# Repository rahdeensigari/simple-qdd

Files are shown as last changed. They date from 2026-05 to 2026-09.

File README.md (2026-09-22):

# simple-qdd
A small and cheap quasi-direct driven planetary robotic actuator. It uses an 8:1 planetary reduction powered by a 5010 BLDC drone motor recoiled in star configuration to get ~100KV.



This is not the first actuator that I have made, and it certainly won't be the last either. I was aiming to design something small and cheap that could still have a decent amount of power. In order to do this, I have to recoil a small motor that is intended to be used for drones to be more optimal for high load applications.

If you are interested in building this yourself, the BOM below is a good starting place for getting materials, but anything will similar specifications will work just as well. You can download the CAD files either directly from the Onshape document (below) or from the files listed in the CAD folder.

[CAD](https://cad.onshape.com/documents/57a8ef0242364670953218e9/w/659145295f694f0fa79f9cef/e/7b9566cf06dc05a88ad73bb1)

# BOM

| Quantity | Name | Vendor | Cost | Link | Notes  |
|---|---|---|---|---|---|
| 1 | 5010 BLDC Motor | AliExpress | $19.66  | https://www.aliexpress.us/item/3256808560627221.html  | |
| 1 | Output Bearing | AliExpress | $4.39 | https://www.aliexpress.us/item/3256807233759178.html  | |
| 3 | Needle-Roller Bearing | MCM | 23.58 | https://www.mcmaster.com/5905K496/ | |
| 7 | M3 Heatset x 3.4mm | MCM | 8.64 | https://www.mcmaster.com/94459A769/ | 1 Pack |
| 3 | M3 Heatset x 5.9mm | MCM | 5.48 | https://www.mcmaster.com/94459A421/ | 1 Pack |
| 1 | ODrive Micro | ODrive | 89 | https://shop.odriverobotics.com/products/odrive-micro | |
| 4 | M3x0.5 8mm FH | MCM | 5.82 | https://www.mcmaster.com/91294A128/ | 1 Pack |
| 4 | M3x0.5 5mm FH | MCM | 5.57 | https://www.mcmaster.com/91294A125/ | 1 Pack |
| 3 | M3x0.5 10mm FH | MCM | 6.36 | https://www.mcmaster.com/91294A130/ | 1 Pack |
| 4 | M3x0.5 10mm BH | MCM | 7.91 | https://www.mcmaster.com/92095A182/ | 1 Pack |
| 5 | M4x0.7 50mm SH | MCM | 15.85 | https://www.mcmaster.com/91290A186/ | 1 Pack |
| 5 | M4x0.7 Nuts | MCM | 13.25 | https://www.mcmaster.com/94645A101/ | |
| | | | $205.51 | | |

NOTE: A bulk of the price is because a lot of the fastners come in packs with way more of the item then is needed.

# Assembly

Main (1)


Use these exploded and section views as well as the CAD link above while assembling. Some important notes, assemble the gear carriage, the bottom retention flange, and the bearing at once before putting it into the motor carriage. Make sure the motor is fully installed in the carriage and the sun gear is installed on the motor before inserting the bearing and gear carriage assembly. Make sure the heat-set inserts in the gear carriage are fully inserted, or else the countersunk bolts won't fit correctly.

If you are going to recoil the motor, use 26 AWG magnet wire with 31 turns-per-slot if you want to get to the same KV I used. Use the following diagram when you are recoiling:


https://youtube.com/shorts/wS8en63CQcI

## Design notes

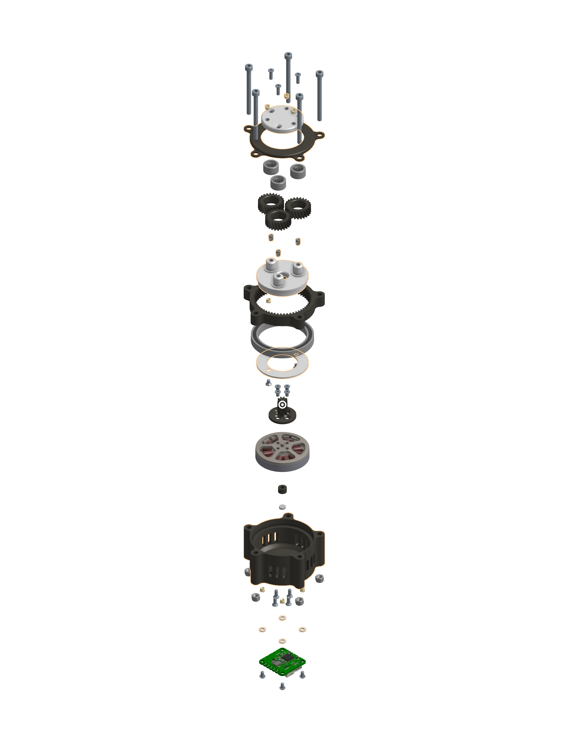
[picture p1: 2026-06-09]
docs/Exploded View.png

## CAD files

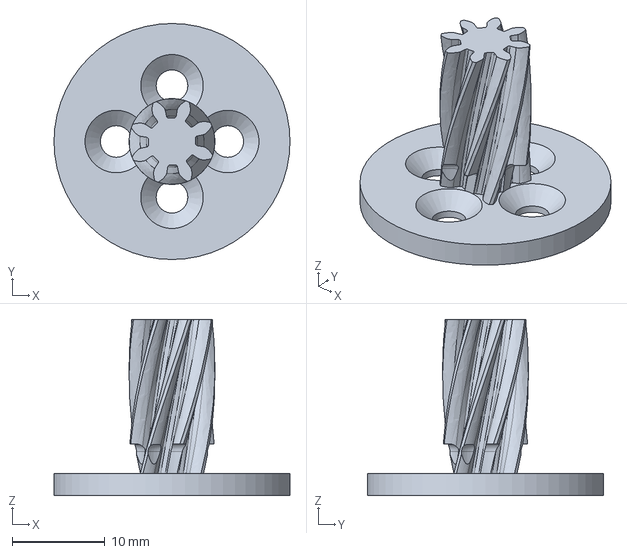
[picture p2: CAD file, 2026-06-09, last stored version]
cad/Sun Gear.step
25.4 x 25.4 x 18.9 mm

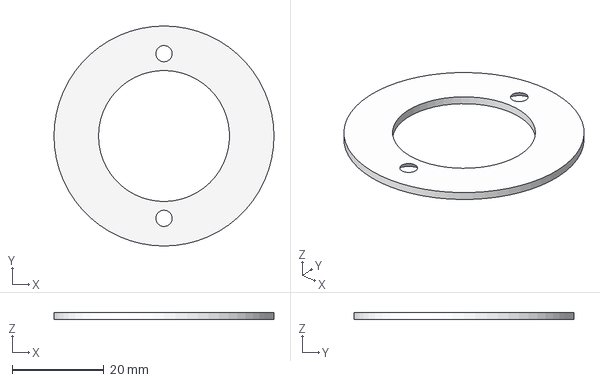
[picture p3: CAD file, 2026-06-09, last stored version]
cad/Bottom Bearing Flange.step
48.0 x 48.0 x 1.59 mm

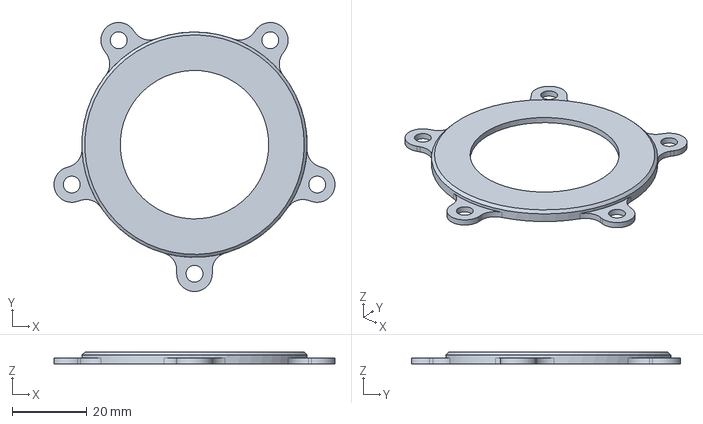
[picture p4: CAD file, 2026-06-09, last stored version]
cad/Top Cover.step
75.2 x 72.0 x 3.17 mm

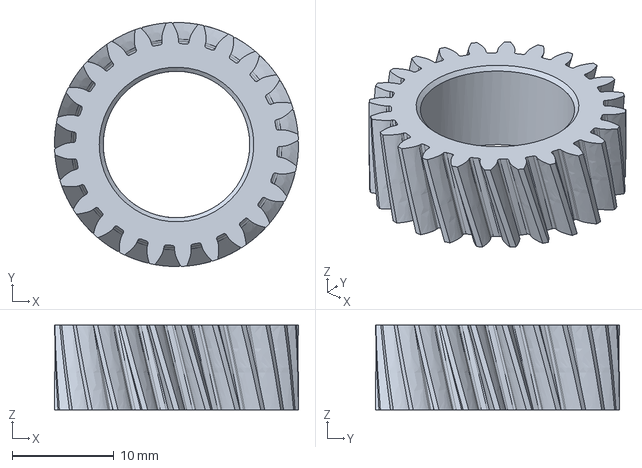
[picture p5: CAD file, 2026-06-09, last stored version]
cad/Planet Gear.step
24.0 x 24.0 x 8.33 mm

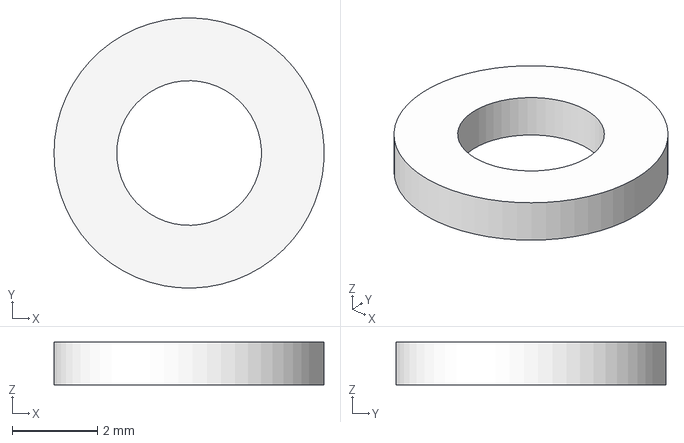
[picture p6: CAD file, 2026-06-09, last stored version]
cad/Spacer.step
6.35 x 6.35 x 1.00 mm

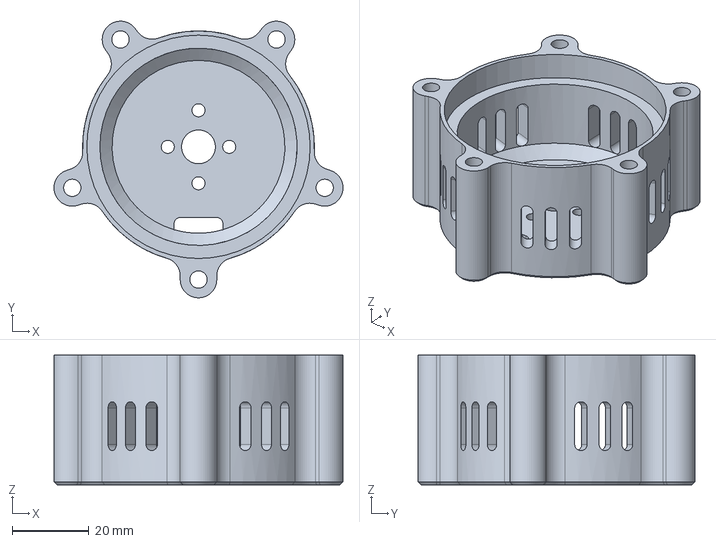
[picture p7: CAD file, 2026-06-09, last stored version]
cad/Motor Carriage.step
75.2 x 72.0 x 33.8 mm

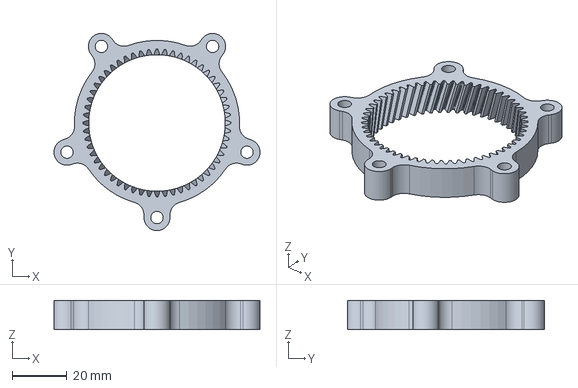
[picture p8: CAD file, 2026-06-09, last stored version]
cad/Ring Gear.step
75.2 x 72.0 x 10.7 mm

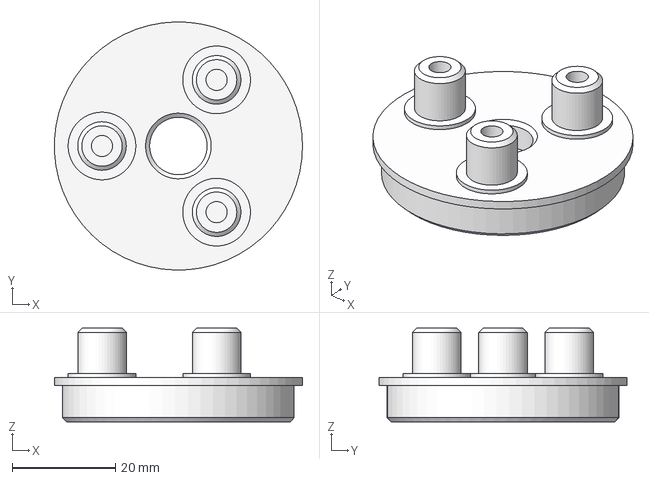
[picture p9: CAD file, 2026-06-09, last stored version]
cad/Gear Carriage.step
48.0 x 48.0 x 18.1 mm

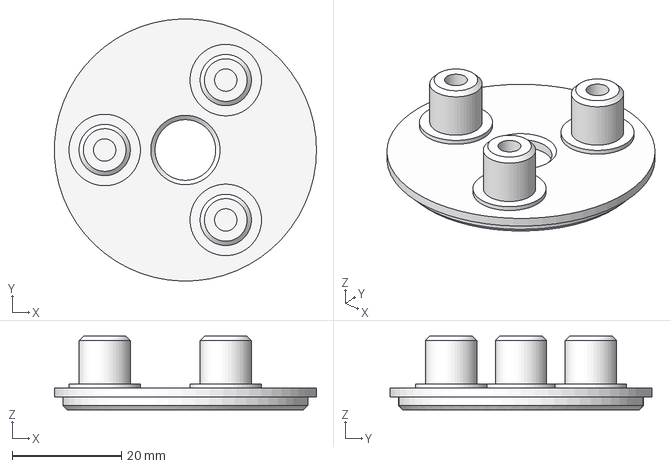
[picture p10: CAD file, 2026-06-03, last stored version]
cad/Gear Carrier.step
48.0 x 48.0 x 13.5 mm

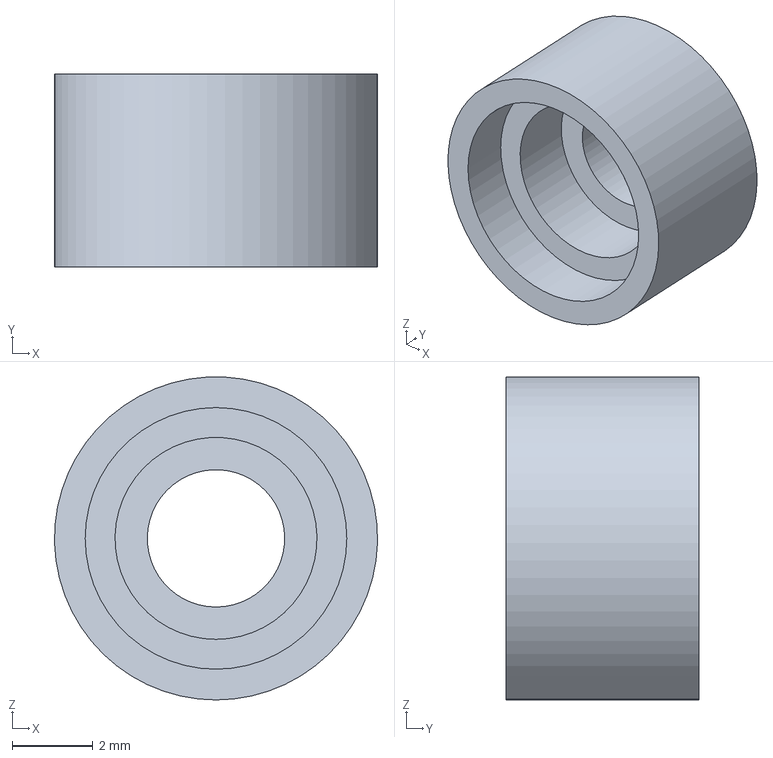
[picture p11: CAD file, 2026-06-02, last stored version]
cad/Magnet Mount.step
8.00 x 4.78 x 7.99 mm

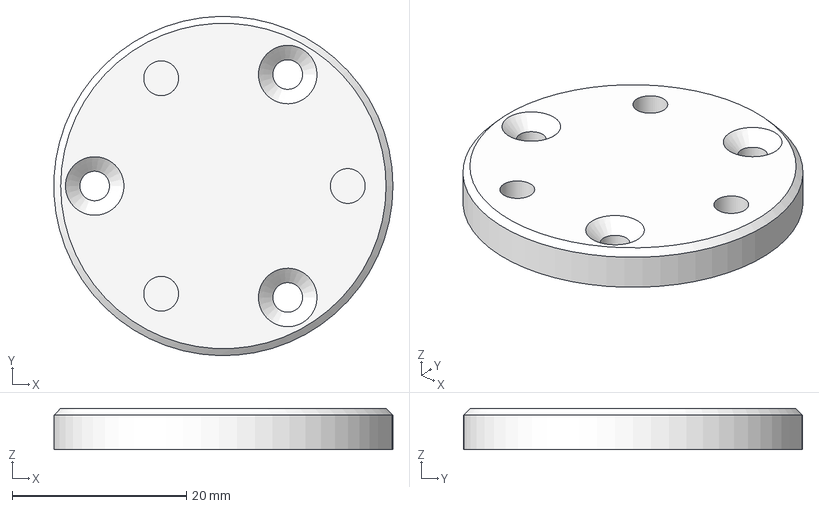
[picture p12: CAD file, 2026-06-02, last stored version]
cad/Output.step
38.9 x 38.9 x 4.76 mm

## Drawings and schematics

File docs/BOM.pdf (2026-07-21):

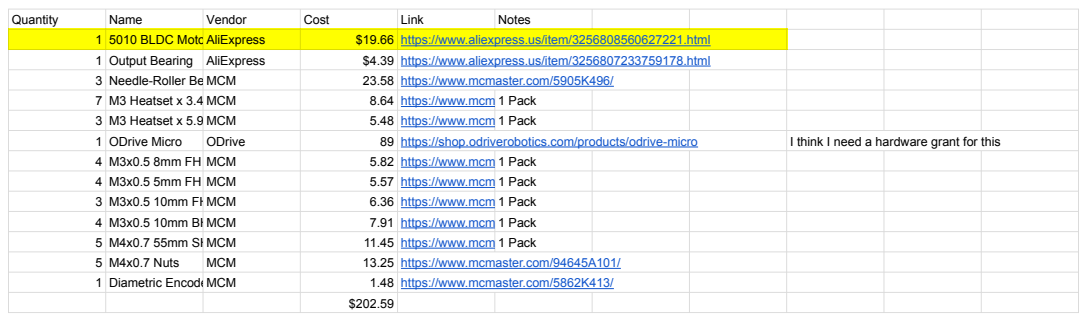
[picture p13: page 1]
Quantity; Name; Vendor; Cost; Link; Notes; 1 5010 BLDC MotorAliExpress; $19.66 https://www.aliexpress.us/item/3256808560627221.html; 1 Output Bearing AliExpress; $4.39 https://www.aliexpress.us/item/3256807233759178.html; 3 Needle-Roller Bearing MCM; 23.58 https://www.mcmaster.com/5905K496/; 7 M3 Heatset x 3.4mmMCM; 8.64 https://www.mcmaster.com/94459A769/ 1 Pack; 3 M3 Heatset x 5.9mmMCM; 5.48 https://www.mcmaster.com/94459A421/ 1 Pack; 1 ODrive Micro; ODrive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

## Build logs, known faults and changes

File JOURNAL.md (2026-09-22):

---
title: "Quasi-Direct Drive Actuator"
author: "Rahdeen Sigari"
description: "A small and cheap quasi-direct driven planetary robotic actuator."
created_at: "2026-05-09"
---

# May 9: Start

Essentially, my goal is to create a full 6-axis robotic arm, but in order to actually do that, I first need to design and build a powerful enough actuator. I've actually already built a similar actuator! Here's a photo:

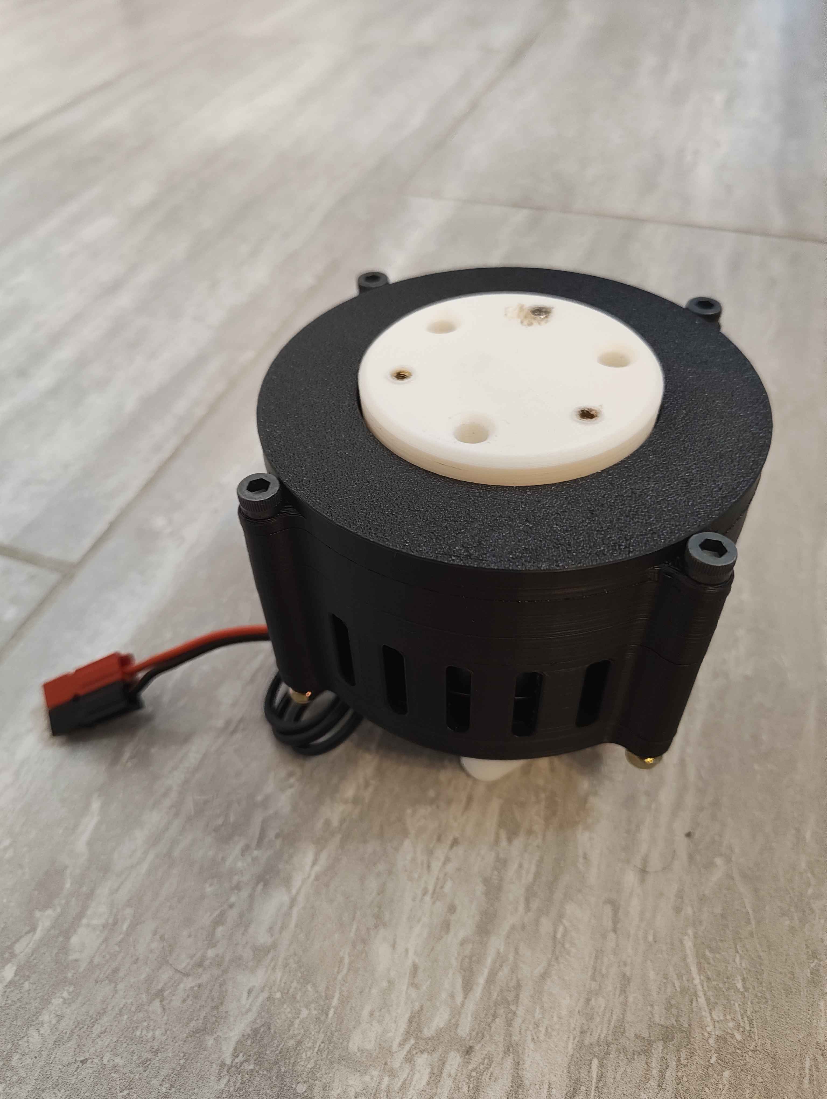
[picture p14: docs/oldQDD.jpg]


The problem with this actuator however is that it is too large, heavy, and expensive to use for an actual 6-axis arm. That's why I'm making this, a smaller, lighter, and cheaper robotic actuator that can still be powerful enough to effectively drive a robotic arm. Specifically, I want this actuator to be at most 3" in diameter.

In mechatronics applications like this, it is important for actuators to be somthing called *Quasi-Direct Drive.* Quasi-Direct Drive (QDD) actuators have a high enough gear ratio so that they can actually move signficant loads while not being so powerful that they cannot be backdriven. This is important as QDD actuators like this can completely eliminate the need for external touch sensors, as the actuator cannot overpower the external forces that are put upon it. This allows for the firmware to detect the resulting current increase and register that it has came in contact with an object.

I was kind of inspired to do this by Aaed Musa's [video](https://www.youtube.com/watch?v=GFLa1b1juUo) of him making another robot dog. He actually used something called a capstan drive, which is a gear reduction achieved by using ropes. Instead, I'm using a planetary gearbox, as it's the cheapest option and the best for small reductions like the ones in a QDD actuator as opposed to something like a cylcoidal drive. What really intrested me though was the hardware he used, specifically the motors and motor controllers. He used the following:

- Makerbase XDrive Mini (motor controller)
- TYI 5008 Brushless Motor

For my old actuator, I used:

- ODrive S1 (motor controller)
- Eaglepower LA8308 KV90 (motor)

Don't get me wrong, the hardware I bought worked excellently, but it would absurd to use them for something like a robotic arm, they're just too expensive. Luckily, the amount of power that I got from my old actuator is way more than I need for my eventual goal of making a robotic arm, as long as I keep everything else lightweight. In comparison, without accounting for extra fees, all the hardware that Aaed Musa used is $177.71 cheaper than what I used, which is absolutely absurd. For the record, if I had tried making a 6-axis arm with my old hardware, it would cost $1066.26 more!

I'm happy with the XDrive Mini as my new motor controller, but not entirely confident in the motor's strength, as it has a very high KV, which is not ideal for QDD actuators. The easiest way to fix this without increasing the gear reduction (which would result in it not being QDD anymore) is to recoil the motor stator, which I would like to avoid if I can. Will do some more research later on any alternative motors I can use.

**Total time spent: 1 hour**

# May 10: Researching Motors

I already established the TYI 5008 as good option, but its problem is mainly that it would need me to recoil the stator to decrease its KV (and subsequently increase its torque) to around 100. Ideally, I'm looking for a motor around 50mm in diameter.

- After a bit of research, I found [this](https://www.rctimer.com/rctimer-gbm5010-150t-gimbal-brushless-motor-p0446.html) motor. It is already 90KV, which means that I won't have to recoil it, but the main problem is that it is most likely too small.
- [Here's](https://rctimer.com/rctimer-5010-260kv-multirotor-brushless-motor40mm-shaft-p0132.html) another one, this one still needs to be recoiled, but the KV is much lower so it will be easier. Kind of slow shipping time though.
- [Another one](https://www.aliexpress.us/item/3256808560627221.html). This one is probably the most promising, its cheap, decent shipping time, and similar specs to the TYI 5008, of course, it will, of course, still need recoiling.

Sadly, thats all I could really find. To be honest, all these motors are pretty similar, but I think I'm going to with the third option, which is a 5010 360KV motor off Aliexpress. If I'm being honest, this is mostly because it ships the fastest out of any of the alternatives, all these motors are either 5010 or 5008 motors, and pretty much all of them except for the first one I found need to be recoiled (translation: I chose the third one based off vibes). I might buy one so that I can test its capabilites.



**Total time spent: 1 hour**

# May 11: Starting CAD (Or not)

Think I'm ready to start actually planning this out in CAD. I found [this](https://grabcad.com/library/bldc-motor-5010-1) CAD model of the motor, its supbar, but it will do for now:



Ok I did a bit more research, and I want to slightly pivot my plans. Instead of jumping straight into modeling this in CAD, I want to buy a motor first and see how well it performs, and also see its actual shape in real life as opposed to the, for lack of a better term, shitty CAD model that I found. This will let me actually CAD effectively instead of guessing. I can still work on the actual gearbox and the output stage while I wait. I've got finals to study for though so I'll save that for another time.

**Total time spent: 35 minutes**

# May 17: CAD Work

I found [this](https://grabcad.com/library/mks-odrive-mini-1) model of the motor controller, the step file that they provided did not work, so I had to import the .dwg file they gave into Fusion 360, then export that as a .step for it to work inside of OnShape:



The problem now is how I'm going to mount everything. Mounting the motor controller is pretty straight forward, really all I need are some heat-set inserts in the base motor casing that I can use to bolt it directly on. The problem is the motor itself. The CAD is very unclear about this (so is the listing on aliexpress itself) but I'm assuming that the shaft in the center of the bolt circle rotates independently from the bolt holes:



Most motors like this have some sort of bearing around the shaft, but it isn't visible in the CAD, and for some reason all the distributors of the motor seem to be allergic to giving any views other than the front of the motor, so I'm hoping this is actually how it's going to function. The best way to mount this is probably to have some countersunk holes on the bottom of the motor carriage, on the same face as the motor controller's heat-set inserts, where I can fasten the motor with some countersunk bolts. Now, for the motor controller to actually find the position that the motor is in, there needs to be a diametric magnet on the motor shaft that the motor encoder located on the back of the controller can read the position of. A diametric magnet is essentially just a magnet magnetized along its diameter as opposed to its vertical midplane. This allows the encoder to read the position of the poles, which translates to the position of the motor. [McMaster-Carr](https://www.mcmaster.com/products/magnets/direction-of-magnetization~through-diameter/) has a pretty large catalogue of diametric magnets. An 1/8" magnet will fit pretty well on the shaft of the motor. [This](https://www.mcmaster.com/5862K411/) magnet meets my specifications pretty well. It's almost the perfect size to fit directly on the shaft. I designed this small 3D printed part to mount the magnet:



I'm going to quickly print it to ensure it can be printed, it's a really small part so I'm concerned if it can be printed or not.



It printed, its so small though that I'm not sure if the parts will actually fit? If not, I will just directly glue the magnet on with a template.

I started making a layout sketch of the entire actuator, what I realized was that in order to keep a 2mm distance from the onboard motor controller and the magnet, there would only be around 1mm of clearance for a countersunk hole... which is not enough. To fix this, I'm using [this](https://www.mcmaster.com/5862K202/) magnet instead, which is a 1/16" taller. I have around 2.5mm of room now, which is definitely enough. Here is the sketch so far:



Alright it's time to talk about the gear reduction I'm using. In the past, I've used 8:1 with success, and I think I'm going to stick with 8:1 for this as well. I would like to use 4 planet gears, but it's not quite possible to get them to fit...



Which is why I'm just sticking with 3. With some playing around, I found that the perfect size for the gears are:

- Sun: 8 teeth
- Planet: 24 teeth
- Ring: 56 teeth

Using all of that, I made a (VERY!!!!) rough layout sketch of the actuator:




I very much expect to change all of this later but for now it's good enough for me to start cadding the actual parts :)

**Total time spent: 2.33 hours**

# May 18: More CAD Work - Physical Parts

I started by starting to make the motor carriage, but I think there's a very big (literally) problem:



As you can see, if I want my motor controller to fit nicely in the actuator profile, I would need to make it much larger in diameter. This would cause it go out of my 3" diameter design constraint. So, the only option would be to find a motor controller with a smaller profile. My first thought was the ODrive Mini. It's more expensive, but it has the same features as the XDrive while being much smaller plus having the added benefit of having a GUI. Another option would be to use a cheaper controller like the moteus-c1 that doesn't have UCB-C compatibility, then making my own CAN to USB-C adapter. The price difference is negligible enough that it's not worth doing that though, so I'm just going to pivot to the ODrive Micro for now. Unfortunately this means I'm going to have to change a lot of stuff. Because of this change, I can actually go back to using a 1/16" tall magnet!

Redid the layout sketch:



Didn't really journal as I was working on it so I'm just to explain what happened. I started modeling the motor carriage. Since there are components under the pcb as well, I had to slightly offset it from the base of the motor carriage. At first, I tried adding a large flange at the bottom, but it still interfered with some of the components at the very edge of the board so I'm just going to use some 3dp spacers instead:



Like I mentioned before, the motor is mounted by some countersunk bolts right below the motor controller. The actual controller is mounted with [these](https://www.mcmaster.com/94459A769/) heat-set inserts. I also started thinking about the gears. I decided to bring the dp up to 22.5 instead of 20 as that allow the pitch diameter of the ring gear to sit slightly further in from the inside of the motor carriage:



The entire assembly so far:



**Total time spent: 2.4 hours**

# May 22: CAD Work + Motor Came

Look what came today!



And, as I guessed, the CAD was inaccurate after all. Turns out where I thought there was just a nub on the bottom on the motor was actually a screw:



Because of this I have to change the magnet mount. I started by updating the CAD to be accurate:



Then I redid the magnet mount:



Then, I made the entire casing smaller, there was a lot of unnecessary extra space between the motor and the casing before that I got rid of:



Because of this, I had to increase the dp of the gears again to 27.5. The gears need a carriage to ride on, and said carriage must be able to rotate freely. This can be done using a large bearing with the carriage riding inside. For my old gearbox, I used [these](https://wcproducts.com/products/WCP-1870) bearings, and they worked wonderfully, so I'm going to continue using those. From here I moved on to modelling the sun gear. However, I encountered a problem very quickly:



The gear itself was blocking the countsink holes. To fix this, I had to have the gear itself snap fit onto the mounting base. I had to spend a lot of time figuring out a shape that I could actually print. This is what I have right now, but I'm definitely going to have to change it:



**Total time spent: 1.75 hours**

# May 24: CAD Work - Sun Gear and Gear Carriage

Continued where I left off yesterday by continuing to iterate on ways to solve the sun gear mounting problem. At first, I tried making another of a snap fit design that could actually reasonably work:



After trying to print it though, it was evident that this was not the solution, as my printer cannot print in enough detail to be able to create small features like these. Because of this, I decided to pivot to a simpler solution, which was to simply raise the gear up vertically, giving some space to get bolts into:



Testing it out, I found that because of the low amount of material at the base, it was very easy for the gear to snap off the mounting base. However, I could actually fit the bolts in the holes now with this modification. To increase the strength at the base, I kept some of the original gear profile intact:



Even with this modification, the gear was still weaker than I'm happy with. For the actual production parts I am definitely going to have to use a more ductile material like PETG instead of PLA, but PLA is fine to prototype with for now. I briefly had a problem of the clearance hole for the motor shaft in the sun gear being too short, but this was a quick fix. Here's what the gear looks like on the motor, I couldn't bolt it in because I don't have the right length flathead bolts:



Noticed this, the motor carriage is interfering with the motor. Very easy fix:



(Forgot to mention this earlier, [this](https://cad.onshape.com/documents/f349bdd78c53f3325055aefc/v/0ca31cd0b35e796be912d9e2/e/53214cbff7d86d5817cf8efb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) is the featurescript I used to generate the gear.

I then started working on the planet gear carrier. First, I made the basic shape. The flange on the bottom rests on top of the x-contact bearing, and the cutout and hole in the middle is to give the sun gear clearance:




**Total time spent: 1.32 hours**

# June 1: CAD Work

First I made the planet gear, just to get a visual of the geometry, I'm going to have to change some things about it.



So here's the problem, there are two solutions to get the gears to move smoothly with as little friction as possible. Either:

- Completely coat the carriage with a lubricant, reducing friction without the need for any external hardware.
- Have the planet gears rotate on bearings to smooth out movement.

Since this project is completely 3D printed, and I want to reduce the mess as much as possible, I'm going to go with the second option of using bearings. Now, here's the actual issue. Bearings are huge. This is what I did in my last gearbox:



The problem is that since I'm reducing the size of my gears, I don't have enough space to fit in a full sized ball bearing set into the gear. To fix this, I need to different type of bearing. I did a bit of research, and I stumbled upon [these](https://www.mcmaster.com/5905K496/) needle-roller bearings. They're technically not as smooth as ball bearings, but with some lubrication they should still work perfectly fine.

With these changes in mind, here is the planet gear I created. Unfortunately, this meant upping the heigt of the gears, and by result, the gearbox. Unfortunately just one of the results of using a stock motor for an actuator:



I then designed these extrusions on the the gear carrier for the planet gears to rotate on. The hole in the middle is for a heat-set insert.



Assembly:



I'm not modelling the motion right now because I really don't care enough to. Here's the ring gear:



Next, I mmade the output plate. There are three countersunk holes to secure it to the gear carriage, as well as three heat set inserts to mount other components to it:



Then, I made a top cover for the entire gearbox. I also added 5 M5 holes to put bolts through in order to secure the entire assembly:



I also added these "vents" so I could see the motor turning + because it looked cool:



Also, I added this wire cutout in the base of the motor carriage, without it there's nowhere for the wires to go:



With that, the CAD is actually complete! I was originally going to add a motor controller cover, but I see no need to as it would just limit my access to the port:



**Total time Spent: 3 hours**

# June 2 - Touchups and Docs

Before I start uploading all my documentation, I printed everything out just for a quick fit check.



Some problems I found:

- M3 clearance holes were too small. (For some reason I had it set to close fit?)
- The actual mounting on the motor weren't aligned with the wires. I'm not going to fix this yet because I'm going to be recoiling the motor anyways.


Everything else seems to be fine right now.

I added some stuff in my README, then created my BOM. A lot of cost comes from the fasteners, but I already have a lot of them.
| Quantity | Name | Vendor | Cost | Link | Notes  |
|---|---|---|---|---|---|
| 1 | 5010 BLDC Motor | AliExpress | $19.66  | https://www.aliexpress.us/item/3256808560627221.html  | |
| 1 | 1.75"" X-Contact | WCP | $34.99  | https://wcproducts.com/products/WCP-1870 | |
| 3 | Needle-Roller Bearing | MCM | 23.58 | https://www.mcmaster.com/5905K496/ | |
| 7 | M3 Heatset x 3.4mm | MCM | 8.64 | https://www.mcmaster.com/94459A769/ | 1 Pack |
| 3 | M3 Heatset x 5.9mm | MCM | 5.48 | https://www.mcmaster.com/94459A421/ | 1 Pack |
| 1 | ODrive Micro | ODrive | 89 | https://shop.odriverobotics.com/products/odrive-micro | |
| 4 | M3x0.5 8mm FH | MCM | 5.82 | https://www.mcmaster.com/91294A128/ | 1 Pack |
| 4 | M3x0.5 5mm FH | MCM | 5.57 | https://www.mcmaster.com/91294A125/ | 1 Pack |
| 3 | M3x0.5 10mm FH | MCM | 6.36 | https://www.mcmaster.com/91294A130/ | 1 Pack |
| 4 | M3x0.5 10mm BH | MCM | 7.91 | https://www.mcmaster.com/92095A182/ | 1 Pack |
| 5 | M4x0.7 50mm SH | MCM | 15.85 | https://www.mcmaster.com/91290A186/ | 1 Pack |
| 5 | M4x0.7 Nuts | MCM | 13.25 | https://www.mcmaster.com/94645A101/ | |
| | | | $236.11 | | |

**Total Time Spent: 1.25 hours**

# June 3 - Bearing Changes

Ok I got some opinions on using the X-Contact bearing, because it is ridiculously expensive, and I've decided that something that high quality is not needed at all. Instead, I found [this](https://www.aliexpress.us/item/3256807233759178.html) bearing on AliExpress. It's slightly different in size, so I had to change some parts to get it to fit properly, but this is definitely going to be the more cost effective option:



Here is the updated BOM:

| Quantity | Name | Vendor | Cost | Link | Notes  |
|---|---|---|---|---|---|
| 1 | 5010 BLDC Motor | AliExpress | $19.66  | https://www.aliexpress.us/item/3256808560627221.html  | |
| 1 | Output Bearing | AliExpress | $4.39 | https://www.aliexpress.us/item/3256807233759178.html  | |
| 3 | Needle-Roller Bearing | MCM | 23.58 | https://www.mcmaster.com/5905K496/ | |
| 7 | M3 Heatset x 3.4mm | MCM | 8.64 | https://www.mcmaster.com/94459A769/ | 1 Pack |
| 3 | M3 Heatset x 5.9mm | MCM | 5.48 | https://www.mcmaster.com/94459A421/ | 1 Pack |
| 1 | ODrive Micro | ODrive | 89 | https://shop.odriverobotics.com/products/odrive-micro | |
| 4 | M3x0.5 8mm FH | MCM | 5.82 | https://www.mcmaster.com/91294A128/ | 1 Pack |
| 4 | M3x0.5 5mm FH | MCM | 5.57 | https://www.mcmaster.com/91294A125/ | 1 Pack |
| 3 | M3x0.5 10mm FH | MCM | 6.36 | https://www.mcmaster.com/91294A130/ | 1 Pack |
| 4 | M3x0.5 10mm BH | MCM | 7.91 | https://www.mcmaster.com/92095A182/ | 1 Pack |
| 5 | M4x0.7 50mm SH | MCM | 15.85 | https://www.mcmaster.com/91290A186/ | 1 Pack |
| 5 | M4x0.7 Nuts | MCM | 13.25 | https://www.mcmaster.com/94645A101/ | |
| | | | $205.51 | | |

**Total Time Spent: 0.58 hours**

# June 4 - Preparing for Recoiling the Motor

Alright first, I actually forgot to include the [diametric magnet](https://www.mcmaster.com/5862K413/) in the BOM, so I quickly updated it to reflect that.

Here's the updated BOM:

| Quantity | Name | Vendor | Cost | Link | Notes  |
|---|---|---|---|---|---|
| 1 | 5010 BLDC Motor | AliExpress | $19.66  | https://www.aliexpress.us/item/3256808560627221.html  | |
| 1 | Output Bearing | AliExpress | $4.39 | https://www.aliexpress.us/item/3256807233759178.html  | |
| 3 | Needle-Roller Bearing | MCM | 23.58 | https://www.mcmaster.com/5905K496/ | |
| 7 | M3 Heatset x 3.4mm | MCM | 8.64 | https://www.mcmaster.com/94459A769/ | 1 Pack |
| 3 | M3 Heatset x 5.9mm | MCM | 5.48 | https://www.mcmaster.com/94459A421/ | 1 Pack |
| 1 | ODrive Micro | ODrive | 89 | https://shop.odriverobotics.com/products/odrive-micro | |
| 4 | M3x0.5 8mm FH | MCM | 5.82 | https://www.mcmaster.com/91294A128/ | 1 Pack |
| 4 | M3x0.5 5mm FH | MCM | 5.57 | https://www.mcmaster.com/91294A125/ | 1 Pack |
| 3 | M3x0.5 10mm FH | MCM | 6.36 | https://www.mcmaster.com/91294A130/ | 1 Pack |
| 4 | M3x0.5 10mm BH | MCM | 7.91 | https://www.mcmaster.com/92095A182/ | 1 Pack |
| 5 | M4x0.7 50mm SH | MCM | 15.85 | https://www.mcmaster.com/91290A186/ | 1 Pack |
| 5 | M4x0.7 Nuts | MCM | 13.25 | https://www.mcmaster.com/94645A101/ | |
| 1 | Diametric Encoder Magnet | MCM | 1.48 | https://www.mcmaster.com/5862K413/ | |
| | | | $206.99 | | |

Anyways, while I wait for this to be reviewed on Forge, I'm going to start doing the calculations on how I'm going to recoil the motor. To review, the motor that I have right now is wired in delta-configuration, which means that the three stator windings are connected in a closed loop that resembles a triangle. Each winding's end is connected to the other winding's beginning, making a continuous circuit. There are a couple advantages of a motor wired in delta-configuration. The main advantage of this type of winding is that it can achieve higher torque at higher speeds as opposed to star-configuration coiled motors. Although this sounds like a good thing, these motors are much less efficient at low speeds, as it draws more current for the same amount of torque. Heat generation is also increased with delta-configuration. They are ideal for high-speed applications, but for a robotic actuator, star-configuration is definitely the way to go.



Star configuration is different as all three stator windings are connected to a central point called the neutral point. This forms a star, or Y shape. The other ends of the windings are then connected to the motor controller. This configuration is better suited to give high effeciency at low speeds, which is why it is ideal for this application. A general rule between delta and star-configuration is that delta-configuration coiled motors have a $\sqrt{3}x$ higher KV then star-configuration coiled motors.



Here's the problem: If I were to recoil the motor with the exact same turns/slot and wire awg as the manufacturer, I would get ~208 KV, which is way higher than what I'm aiming for. Luckily, the KV rating is proportional to the number of turns/slot on the motor. So I can divide $208/100$ (100 being the KV I'm aiming for) to get $2.08$. This means that I have to use $2.08x$ the turns/slot to get to 100KV. Since the windings are layered on top of eacher other on my motor, counting the turns/slot is going to have to require taking apart the winidngs, so first, just to make my calculations more accurate, I'm going to find the actual KV of the motor to see if it's accurate or not. To do this I'm going to use the following formula:

$KV=RPM/(V*\sqrt{3})$

I'm multiplying the voltage by $\sqrt{3}$ because the motor is currently coiled in delta configuration. Normally you would use something like a lathe or a drill for this, but I don't have access to anything like that so I'm just going to use the motor from my old actuator. I had this old test mount laying around that I'll use:



Then I wrote this quick script to set the motor to a desired RPM:

```python
import odrive
import time

from odrive.enums import *

odrv = odrive.find_any()
axis = odrv.axis0

axis.controller.config.control_mode = ControlMode.VELOCITY_CONTROL
axis.controller.config.input_mode = InputMode.PASSTHROUGH
axis.requested_state = AxisState.CLOSED_LOOP_CONTROL

axis.controller.config.vel_limit = 30.0

time.sleep(0.5)

def set_rpm(axis, rpm):
    turns_per_sec = rpm / 60.0
    axis.controller.input_vel = turns_per_sec

def get_actual_rpm(axis):
    turns_per_sec = axis.pos_vel_mapper.vel
    return turns_per_sec * 60.0

set_rpm(axis, 500)

try:
    while True:
        print(f"Target: {axis.controller.input_vel * 60:.1f} RPM | "
            f"Actual: {get_actual_rpm(axis):.1f} RPM")
        time.sleep(0.1)

finally:
    print("Stopping motor...")
    axis.controller.input_vel = 0.0
    time.sleep(0.5)
    axis.requested_state = AxisState.IDLE
    print("Motor Stopped")
```

Alright I'm going to be honest I restarted my computer and lost an hour of progress on the journal... So if the following stuff I write isn't as detailed that's why.

I'll quickly go over how the script works:

```python
import odrive
import time

from odrive.enums import *

odrv = odrive.find_any()
axis = odrv.axis0

axis.controller.config.control_mode = ControlMode.VELOCITY_CONTROL
axis.controller.config.input_mode = InputMode.PASSTHROUGH
axis.requested_state = AxisState.CLOSED_LOOP_CONTROL

axis.controller.config.vel_limit = 30.0
```

This block is the setup. I'm importing the ODrive pip module and time, then importing all the enums from the module. Then, I'm searching to see if any ODrive boards and connected and assigning the motor to axis0. In the last 3 lines, I'm setting the control mode to velocity, the input mode to passthrough, which allows me to control it directly, and setting the axis state to closed loop control. I also set the velocity limit to 30 because by default it was capping me to 600 rpm. I'm pretty sure after you run this once, you don't need that line anymore but I kept it just incase.

```python
time.sleep(0.5)

def set_rpm(axis, rpm):
    turns_per_sec = rpm / 60.0
    axis.controller.input_vel = turns_per_sec

def get_actual_rpm(axis):
    turns_per_sec = axis.pos_vel_mapper.vel
    return turns_per_sec * 60.0

set_rpm(axis, 500)
```

The time.sleep is to give me a second before the motor start spinning. I defined two functions next, one to set the rpm that the motor will be rotating at. I have to divide by 60 because ODrive doesn't handle velocity in RPM. I'm then setting the input velocity to that new value. The get_actual_rpm function gets the encoder reading of the motor. This is to detect if there are any great disparities between the value I set and the actual RPM. I then set the RPM of the motor using the set_rpm function.

```python
try:
    while True:
        print(f"Target: {axis.controller.input_vel * 60:.1f} RPM | "
            f"Actual: {get_actual_rpm(axis):.1f} RPM")
        time.sleep(0.1)

finally:
    print("Stopping motor...")
    axis.controller.input_vel = 0.0
    time.sleep(0.5)
    axis.requested_state = AxisState.IDLE
    print("Motor Stopped")
```

This final block constantly prints the RPM I set the motor to run at and the actual RPM that the encoder detects. It's in a try-finally block because the ODrive module doesn't have a way to deal with the script being terminated by default. Honestly I didn't really need to write a script for this, I could've just used the GUI, but I needed to learn how to code for ODrive anyways so I don't mind.

I quickly modelled an adapter and test stand in CAD that allows me to connect the LA8308 (the golden motor) to the 5010 so I can test the KV. The prongs on the adapters catch each other and rotate:




This is full setup with everything printed:



I was kind of confused at first when I initally ran the motor because I had the multimeter on detecting DC current, so it was just reading 0, but after some reaearch I realized what I did wrong so I switched the multimeter to AC and tried getting readings. I tried running the motor at different RPM's to see if the results varied. Here are the results. I tried every combination of phase wires to get the most accurate result.

1000 RPM
- 1: 1.7V
- 2: 1.7V
- 3: 1.7V

500 RPM
- 1: 0.7V
- 2: 0.7V
- 3: 0.7V

1500 RPM
- 1: 2.7V
- 2: 2.7V
- 3: 2.7V

Here is the KV rating I calculated for each speed:
- 1000 RPM: 340 KV
- 500 RPM: 413 KV
- 1500 RPM: 320 KV

There's a huge difference between the values, especially at 500 RPM. This might be because it's just too slow, so I'm going to delete that data point and try again at 2000 RPM. I got 3.1V all around using 2000 RPM, which translates to 372 KV. Still a bigger difference then I would have liked, but it's not as bad anymore. Taking the average of all three values gives me 344, so not exactly 360 as the manufacturer listed. I'll be using this value for my future calculations. Now that I have the actual KV of the motor, I can go ahead with starting to take it apart.

**Total Time Spent: 3.65 hours**

# June 5 - Recoiling Calculations + Uncoiling Motor

Alright, so I completely uncoiled the motor:



As I was uncoiling it, I counted the amount of turns-per-slot and got 23. Since the KV of the motor is proportional to the turns-per-slot, I can now calculate how many I need to get 100KV:

First I need to account for the motor being in delta configuration:

$344/\sqrt{3}=199$

Then, If I divide that by the KV I want, I get the ratio of how many times more windings I need to get to my desired KV rating:

$199/100=1.99$

$1.99*23=45.8$

45.8 then rounds up to **46**, the turns-per-slot necessary.

**Total Time Spent: 0.35 hour**

# June 6 - Recoiling Attempt #1 + CAD Fixes

I got some cheap 24 AWG magnet wire today, and I tried to recoil the motor using the following diagram:



However, I believe that 24 AWG is too large of a diameter, so I am going to return the spool I got and try 26 AWG instead.

Also, I got some feedback on my design and have a couple changes to make. First, with the current design I can straight up just pull the output disc and the entire gear system will disengage from the main bearing. To fix this, I'm going to add a flange underneath the bearing as well secured by a plastic threading screw.



Here's it implemented:



I decided to not use plastic tapping screws and just use regular screws and heat set inserts as it would be cheaper.

**Total Time Spent: 1.28 hours**

# June 8 - Rewinding Attempt 2

May god help me because this is the most painful process of all time. Obviously I couldn't record journal entries as I was winding the motor, but I basically tried the same thing as before except with 26 AWG wire instead. The good news is that I can actually fit 46 windings in one slot, the bad news is that it was extremely messy and extremely difficult to wind, especially if I was winding a slot that already had another fully winded one right next to it. I technically got an entire phase wired, but I am very unhappy with the result, and I am most likely going to unwind it again. Another possible idea I have is to take out the center bearing stack by heating the adhesive holding it and the stator together. This will making rewinding the stator much easier. Here a couple photos I took of the rewinding process:






**Total Time Spent: 1.73 hours**

# June 9 - Exploded View

The project got returned because I didn't have any assembly instructions, so I'm just going to really quickly make an exploded view showing how everything fits together. Here it is, as well as a section view:

Main (1)


I'm also going to add them to the README and add a quick paragraph laying out some important points. I also updated the CAD folder with the new step files.

**Total Time Spent: 0.55 hours**

# June 19 - Added full STEP file + Updated BOM

Project got returned because I didn't have a full STEP file of the assembly included. I added it as Main.step in the cad folder. Also, because of some earlier changes I made, the retention bolts were too short so I had to up their length to 55mm. I then updated the BOM to reflect that change.



**Total Time Spent: 0.1 hours**

# July 4 - Recoiling Work

Alright, I'm back to work on this after forever! So, here's what I'm going to do. Right now, 46 turns is essentially impossible to get on the motor stator, so, unfortunately, I am going to have to settle for less turns. Instead of trying to go for 100KV, I'm instead going to settle with 150KV. Doing the calcuations again, I need around 31 turns per slot to achieve this. With that in mind, I tried recoiling one phase of the stator. It was still slightly difficult and I had to redo some individual slots a couple times but I eventually got this:



As you can see, I slightly messed up which stator slot I had to route on the last two, but it proved regardless that 31 turns were much easier to route than 46. Luckily, I was going to recoil at least the last slot anyways so it wasn't too big of a deal. I'm going to fix the mistake and continue recoiling tommorow hopefully.

**Total Time Spent: 1 hour**

# July 21 - Clarification for Reviewers

Hello, someone dm'd me on slack about this so I just want to clear it up here. Look at the PDF BOM in the docs folder please, not the CSV or the one in the readme. The parts highlighted (so just the motor for now, and potentially the ODrive if that's not applicable for funding) do **NOT** need funding, I already have the motor, as I needed to buy it beforehand to actually get the dimensions for the CAD model.

**Total Time Spent: 0 hours**

# July 23 - Starting to Build

I got my grant yesterday and ordered all of my parts. McMaster-Carr has extremely fast shipping so all of the parts from them already arrived!



If you remember, I already have all the parts printed, so I just immediately started the build. First, I put the needle bearing in the gears. The clearance was nice, so they fit in perfectly:



Next, I'm going to use my soldering iron to put all the heat-set inserts in. I encountered a pretty big problem while doing this, my heat-set insert tip on my soldering iron is very dirty, so dirty that melted plastic that it caught would get stuck in the threads of the heat-set inserts, basically making them useless. Luckily, I have an M3 tap so I literally just retapped the heat-sets, it's kinda rough but it should do. I am also going to reprint and re heat-set the output disk in white.



One more thing, there's a lot of play between the needle bearings and the internal shaft on the carriage, so I think I'm going to reprint that as well. I'm honestly just going to make that white PLA as well, I doubt that needs to be PETG-CF. As you can see, I originally subracted 0.005" so that it would fit, but this was clearly unnecessary.



I'll write a new journal entry once everything gets printed.

**Total Time Spent: 1.1 Hours**

# July 24 - Change to Gears + Assembly

Alright, so this change was from yesterday but I didn't record it, but I added a little base to the planet gears to help retain the bearings in place, as the bearings were actually slightly shorter than the gears.



With this change and all the ones from yesterday, I printed all of the parts, the gears out of PETG-CF, and the carriage and output disk out of white PLA. Then, I added heat-set inserts to all the parts that needed them and put the needle bearings into the new planet gears. Taking out the needle bearings out of the old gears was quite difficult, as they were retained very well in place, but I eventually had the idea to heat up my 3D printers bed to loosen the filament and push them out.



I also assembled the carriage with the parts that I had available. Everything rotated decently smoothly, but it will be even better with some white lithium which I will put on during the final assembly.



And for good measure, I assembled the entire shell together.



I also updated the github repo with these parts. All that's left to do now is finish rewinding the motor and wait for the other parts to arrive.

**Total Time Spent: 1.22 Hours**

# August 7 - Bearings arrived, carriage changes, recoiling

I forgot to journal most of this stuff earlier so a quick overview of what happened:

First, my bearings came!



Here's the problem: Currently in the CAD I have a slight clearance fit between the gear carriage and the bearing itself. This was done to account for 3D print inaccuracy and tolerances, however I am willing to bet that the bearing was manufactured with unilateral negative tolerances. To fix this, I am going to change the fit of the carriage to be a slight interference fit instead of clearance. I went ahead and printed it out as well. While I'm waiting for it to finish printing, I'm going to try to recoil the stator again. I've been putting this off for a while because of how annoying of a process it is, but I think I just have to bite the bullet and get it done with. Last time I tried to recoil the stator, I accidently coiled the wrong stator slots on one side, so first, I need to redo those two slots:



From there on it went pretty smoothly. Here's the second phase:



And finally the third:



Once all the phases were coiled, I soldered all their ends together at one central star point (since this is now in star configuration):



Then I soldered all my wires on and wrapped them in heatshrink:




After this, I connected the motor to my old ODrive S1 like I did earlier. For some reason, I am getting the error "PHASE_RESISTANCE_OUT_OF_RANGE" when I try to calibrate the motor. I'm really tired right now so I'll pick up trying to fix this tomorrow.

**Total Time Spent: 2.9 Hours**

# September 20 - CAD Changes

It's been a while since I've worked on this, but it seems like for some reason a lot of my journal entries are gone? A lot of stuff happened after the last journal entry, so I'm just going to quickly go over everything. The error from the last entry was fixed through some changes in the ODrive settings, and with those settings changed, everything worked fine (I believe I changed the phase resistance value in ODrive configuration to a value that I measured, but again this happened a while ago so I don't quite remember). After I got the motor to work, I tried to assemble everything, here are a couple photos:






When I tried backdriving the actuator after assembling it, the sun gear actually snapped from the base and there was way more friction then I anticipated:



I believe this happened because I didn't account for the axial thrust force that helical gears generate. I'm going to fix this today by switching to either spur or herringbone gears. I also got my design review by a couple of people and I have a general idea of some other changes that I want to make.

The first thing I did was to make all of the gears spur gears. I started with the sun gear, and this was pretty straightforward. Having it be a spur gear also made making the cutouts for the screws much easier:



The bad thing was that this broke a LOT of my features, but most of these were just changing the reference:



The other gears were also really straightforward, nothing really noteworthy except for having to change more references:



I also had to update the assemblies to match:



The next issue was that there was no clearance between the planet gears and the output disk:



I was initially going to print separate washers entirely to space them apart, but instead I decided on a different approach and just added spacers fused to the bottom of the output disk:




I also went ahead and beefed up the base of the sun gear with some extra material:



Honestly, that's all the changes that I can realistically make while still staying in scope. There's a lot of stuff that I want to change but can't quite do right now, but I will certainly keep in mind when designing another actuator like this in the future (credit to BitSentinel and Eliot):

- An output bearing at the top of the actuator as well as one for the carriage.
- Using a bigger motor controller like I planned on doing before.
- Heatsinking for the motor controllers and the motor.
- Needle bearings must be rolling on a hardened steel shaft, not a 3D print or even an aluminum part.

For now though, I think these changes will be sufficient. I'm going to go ahead and print out all of the changed parts.

First, the output disk. I'm printing this first because I already have white filament loaded on my printer. I'm going to be using 5 walls, 30% gyroid infill for this part and print it out of basic PLA:




Next, I printed all of the changed gears. I'm also going to be printing these with 5 walls, 30% gyroid out of PETG-CF:


(I printed the other two gears later)

I also went ahead and added heatsets to the output disk while I was waiting for everything else to print:



Once everything printed, I first started by putting on the new sun gear. One of the bolts didn't align for some reason? But it works fine so I don't care too much:



Then, I bolted the motor into the body of the actuator:



And assembled the carriage:





I then proceeded to add the needle bearing carriers to the new gears. Getting these on were a pain, I literally had to use the bottom of a water bottle to press them in:



After I assembled these on the carriage, I noticed something a bit weird, and that was that for some reason the sun gear and the planets didn't line up? I have no idea why this is happening, because its not like that in the CAD, but I've checked and it won't effect the performance so I don't really care enough to change it:



Ok HUGE problem, and I think this is what actually caused the ridiculous amount of friction earlier. Turns out I do not know how planetary gears work. When I tried to assemble the ring gear on top of the carriage, the ring gear simply did not fit. This is because the sum of the teeth on the ring gear and the teeth on the sun gear (64) divided by the amount of planet gears (3) did not yield a whole number, meaning that the angle spacing between the planets has to be different or else the ring gear will not fit (credit to waitimoated for helping me find this). To fix this, some CAD changes were obviously necessary. Instead of offsetting the angle of the gears, I just decided to change the teeth count as a whole. I switched to 9t for the sun gear, 63t for the ring gear, and 27t for the planets, as well as a DP of 30.



This was a pretty easy change, luckily most of my CAD is parametric. I did have to redo the weird things with the sun gear but that was pretty straightforward:



I'm going to print these out with the same settings as before, hopefully they work:



**Total Time Spent: 2.28 Hours**

# September 21 - Printing and Testing Changes:

All the gears have been printed. Honestly, I might reprint these because my PETG-CF is too wet and its causing a lot of stringing. The problem is that I don't have a filament dryer so I literally need to use my oven.



I also had to reprint the gear carriage since it changed along with the gears:




Even with the changed gear, it seems like the sun gear is still too big to fit. This is really weird because it worked fine with helical gears, but not with spur? I tried a lot of stuff to fix this, but what eventually worked was to bump up the side length reduction of the gears, make the layer height smaller, and switch to PLA. There's a lot of backlash now, but the gears align perfectly and spin almost frictionlessly:



Now that I fixed that problem, I can move on with the rest of the assembly like normal. First, I had to transfer the heat-sets from the old gear carrier to the new one:




Next I assembled the rest of the gear carrier. To get the black retention lip to fit flush against the carrier, I had to sand the spots where I added heat-sets down to be flush:




I bolted the new sun gear to the motor. Again, one of the bolts were kind of weird, but it works so I don't care:



Then I added the carriage and the planet gears:



Also added the ring gear. I added white lithium grease as well to make it smoother:



Added the top cover and bolted everything in:



Then, finally, the output disk:



When I first back drived the full assembly, I was actually shocked by how little friction there was. I would definitely say that mechanically, this actuator was a success. With that out of the way, I proceeded to add the ODrive. Turns out, the button head screws that I ordered were the wrong size, meaning that I had to actually use flathead screws instead. This was a little bit scuffed, but it worked fine:



Added the phase wires:



This is kind of weird. For some reason, the ODrive is not reacting to the power supply input at all. I used my multimeter to test all of the connections and I've narrowed it down to a problem with the ODrive. After taking it off the rest of the assembly. I think I've identified the problem. It seems like my solder joints were too weak to effectively carry current, so with some help from my Dad, I redid the solder on these pads:



After putting everything back on, that seems to have fixed the problem, and I am now ready to test:




Alright, here's what happened:
- The actuator does spin!
- I can feel that the motor is getting hot through the ventilation holes, this is expected.
- The motor itself was vibrating violently. This was likely due to a mistake with my windings, I'm guessing that I accidently added one more coil on a slot than I was supposed to, causing vibrations.
- The motion of the output disk itself was actually decently smooth.

[Here](https://youtube.com/shorts/wS8en63CQcI) is a video of it working.

With that, I think that I can wrap this project up, and overall I would consider it a success. While it did not work as smoothly as I anticipated, mechanically, I got the actuator to be very robust, and I learned how to recoil a motor if I ever need to do that again.

**Total Time Spent: 2.64 Hours**
